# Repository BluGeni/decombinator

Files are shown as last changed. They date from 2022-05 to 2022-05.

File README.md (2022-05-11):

# Lock Decombinator

From [NerdLab Projects](https://nerdlabprojects.com/projects/8)

May 9, 2022

Step screenshot

> *Updated at: May 10, 2022*

A fun exercise to brute for a master lock combination if you forgot it.

This has been an idea of mine that I have wanted to build ever since forgetting a combo for one of my locks. Yes I know there are ways to limit the amount of combinations down to a manageable amount, but what fun is that?

### Tools Used:

 * 3D printer - I have an old modified Maker select
 * [Cheap Hobby File Set](https://amzn.to/3KXW656)
 * [Hatchbox PLA filament](https://amzn.to/3Pak0h6) (my preferred filament)
 * [Soldering Iron](https://amzn.to/3w6ndXP) - I really like the cordless version from Hakko
 * Allen wrench - 2.5mm (optional)

### Materials Used:

 * Masterlock combination lock ([If you don't have one and want to buy a cheap $3 one](https://amzn.to/38brHDk))
 * [Jumper wires](https://amzn.to/3w86KAQ)
 * [OLED I2C Display Module](https://amzn.to/3FsKS7H)
 * [ELEGOO UNO R3 Board ATmega328P](https://amzn.to/3KXThBf)
 * [MG996R 55g Metal Gear Torque Digital Servo Motor](https://amzn.to/3snNUEW)
 * 3 buttons/switches (If you dont have these on hand, [here](https://amzn.to/3kTEJrH) is an assortment package.)
 * 2x 10k resistors (More resistors than you will ever need [here](https://amzn.to/39BDNWr).)
 * [Perf Board](https://amzn.to/3L1ywo6) or any [bread board](https://amzn.to/3LXjiSo)
 * [Cheap stepper motor with driver](https://amzn.to/3kVdkWo)
 * 2x m3 hex bolt and nut - [Great variety pack](https://amzn.to/3vXJ6Ze)

### Files:

 * [Decombinator v44.f3z](./physical/Decombinator%20v44.f3z)
 * [Decombinator v44.step](./physical/Decombinator%20v44.step)
 * [Base.stl](./physical/Base.stl)
 * [servo mount.stl](./physical/servo%20mount.stl)
 * [Stepper Mount.stl](./physical/Stepper%20Mount.stl)
 * [Plunger.stl](./physical/Plunger.stl)

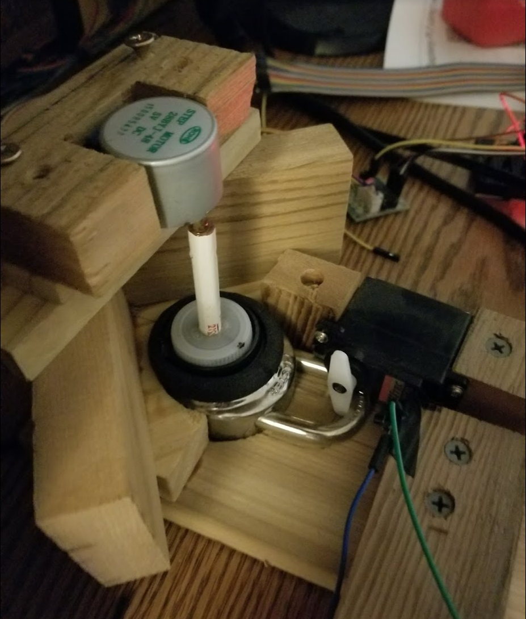
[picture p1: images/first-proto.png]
First prototype


Very first prototype from years ago that was more or less a fail do to lack of programming/design/building skills

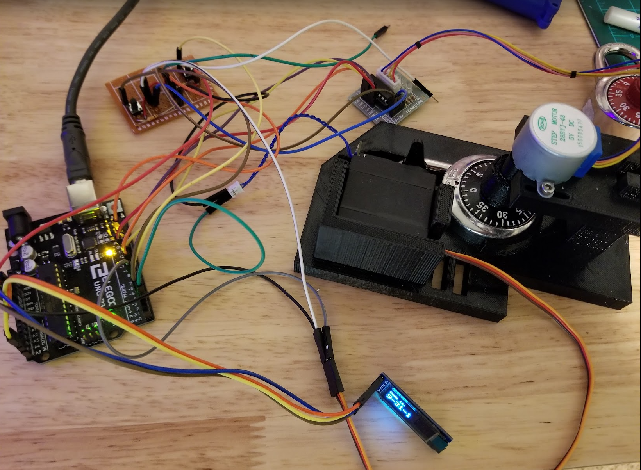
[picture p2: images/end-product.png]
Current iteration


New successful end product 

### Opening a lock

https://www.youtube.com/watch?v=IJM78OVHWlk

### Perfboard

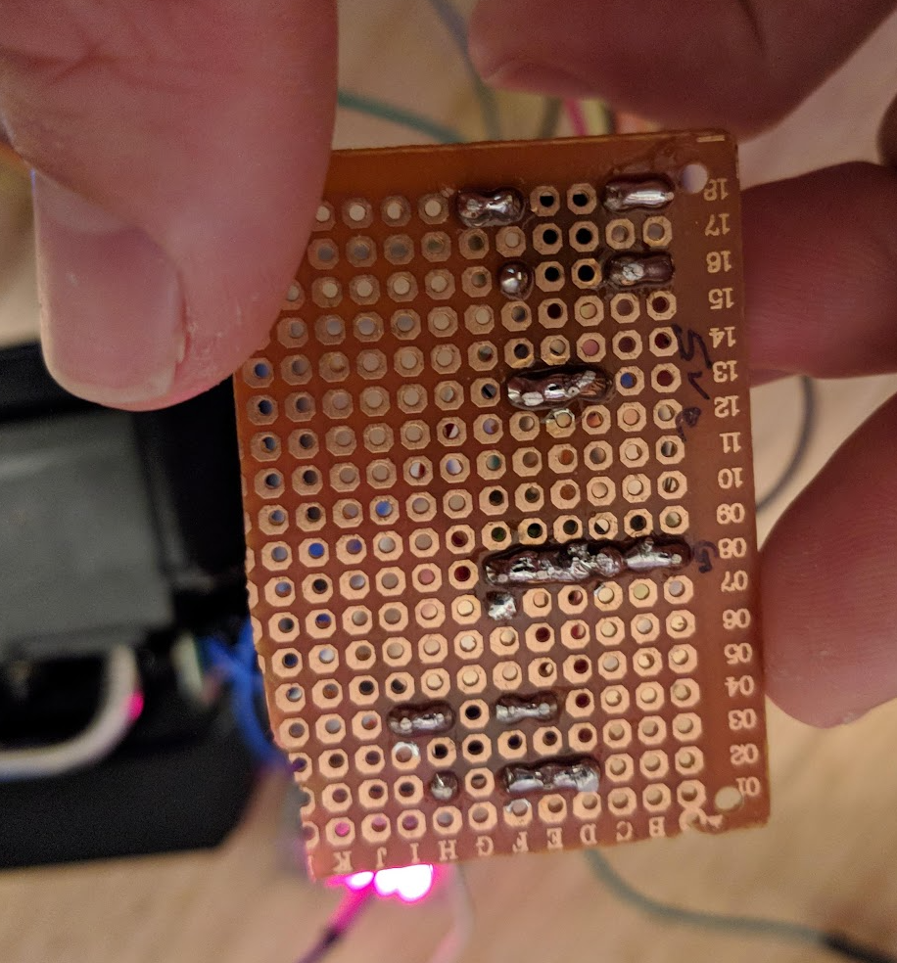
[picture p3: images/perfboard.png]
Perfboard


### How to use

After wiring it all up and starting the Arduino, use the right button switch to move the combo until it is on 0. Once there, you will click the other switch to start the decombination. The LCD screen should show which combo it is trying and display the last combo tried if it opens the lock.

### Circuit

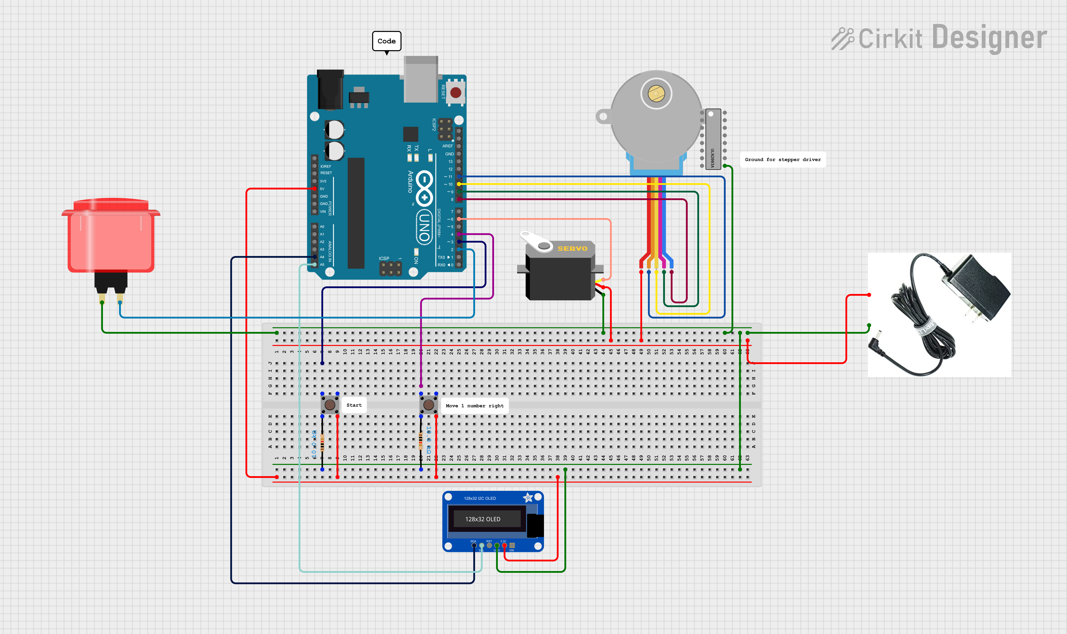
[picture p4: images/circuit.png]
Circuit


### Building

Browse to your Arduino sketch directory, and clone this repo into a subdirectory called `decombo`, e.g.,

```bash
cd ~/Arduino
git clone https://github.com/BluGeni/decombinator.git decombo
```

Then, launch Arduino, load up the `decombo` sketch from your sketchbook, and click "Verify".

> Note: [VSCode can be configured to have way more passive dev-friendly features for Arduino](./VSCode.md).

### Things learned/Struggles:

 * Pins 2 and 3 are the only pins you can use for interrupts.
 * There are 2038 steps per rev in the stepper motor I used - not 2048 like some tutorials said.
 * If your stepper motor is not super strong, attempting to open the lock will sometimes move the number a half number.
 * Ran into a lot of memory issues with all the combinations as a String array.  [Fordi](https://github.com/Fordi) helped me solve that.

References:

* https://jonwestfall.com/wp-content/uploads/2007/08/mlock1.pdf
* https://epow0.org/~amki/car_kit/Datasheet/ELEGOO%20UNO%20R3%20Board.pdf
* https://www.youtube.com/watch?v=l9Kbr8cPqOE - soldering perfboard

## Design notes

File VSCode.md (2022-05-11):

# How to use VSCode with Arduino

1. Have Arduino installed.  This is straightforward on Windows and OS-X.  On Linux, download the tarball and extract it to `/opt`, e.g.,
    ```bash
    sudo tar -C /opt -xJvf arduino-1.8.19-linux64.tar.xz
    ```

2. In VS Code, hit `<Ctrl+Shift+X>`, search for, and install:
    * `vscode-arduino`

3. *Linux*: Hit `<Ctrl+,>` to load up settings, click the "Open Settings (JSON)" button at the top-right, and add the following (version number may be different for you):
    ```json
    "arduino.path": "/opt/arduino-1.8.19",
    "arduino.commandPath": "arduino"
    ```

4. Close VS Code
5. Open this sketch's directory in VS Code, then open `decombo.ino`
6. On the bottom bar, you'll see `<Select Board>`, click it and pick your board (or any board, really).
7. Verify / compile the `ino` file by pressing `<Ctrl+Alt+R>`.

At this point, VSCode should be set up to work on Arduino code.  You'll get redlines, be able to `<F2>` rename identifiers, `<F12>` lookup definitions, `<Shift+F12>` find references, auto-manage git stuff, etc.

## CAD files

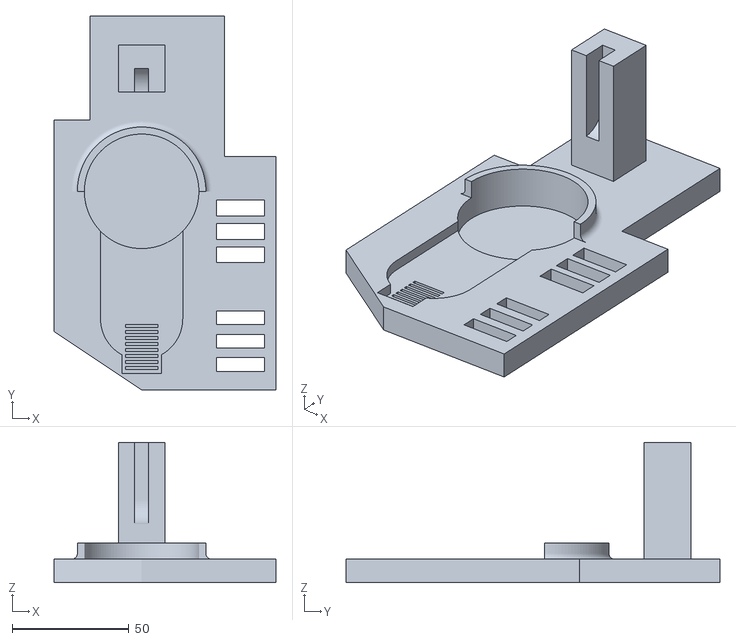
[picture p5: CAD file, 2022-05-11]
physical/Base.stl
95.0 x 160.0 x 60.0

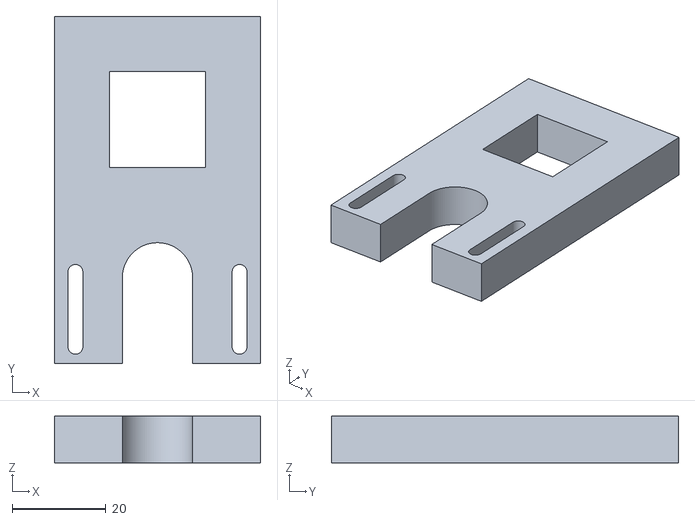
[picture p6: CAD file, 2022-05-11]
physical/Stepper Mount.stl
44.0 x 74.0 x 10.0

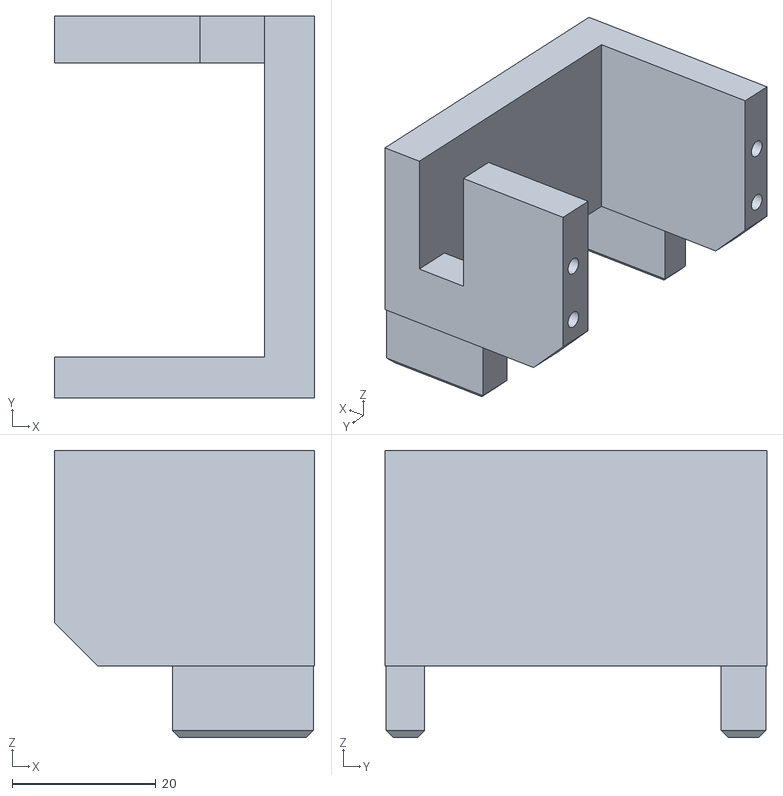
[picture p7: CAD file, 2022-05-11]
physical/servo mount.stl
36.3 x 53.2 x 40.0

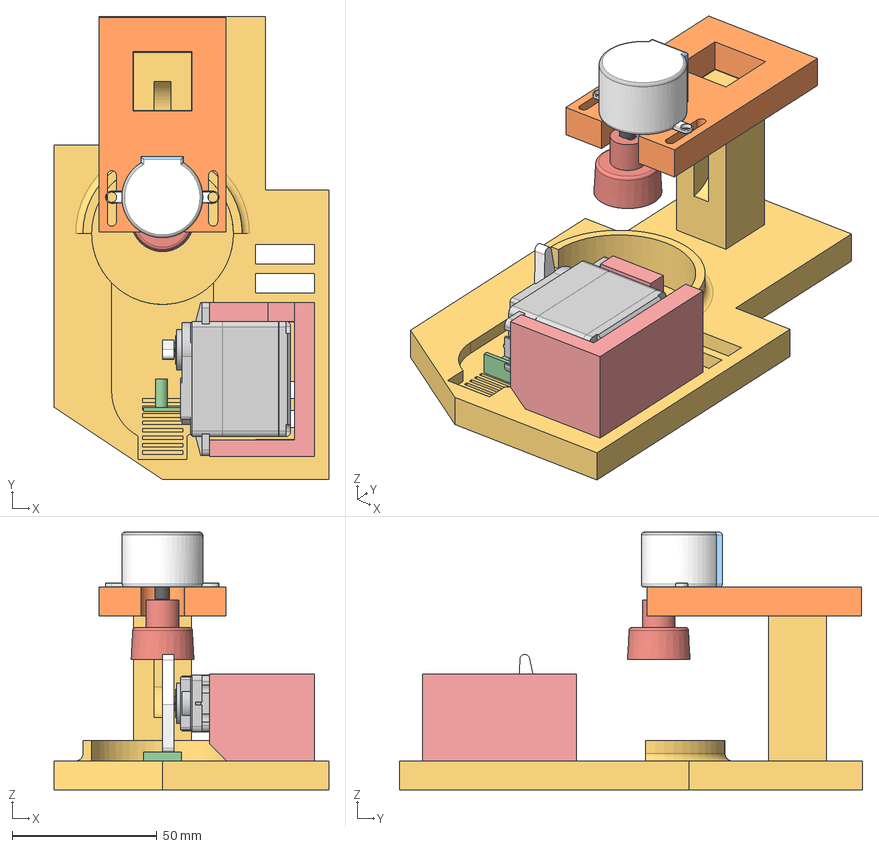
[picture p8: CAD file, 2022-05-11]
physical/Decombinator v44.step
95.0 x 160.0 x 89.0 mm
servo mount
Stepper Mount
Plunger
Slide button
Servo attachment
Base

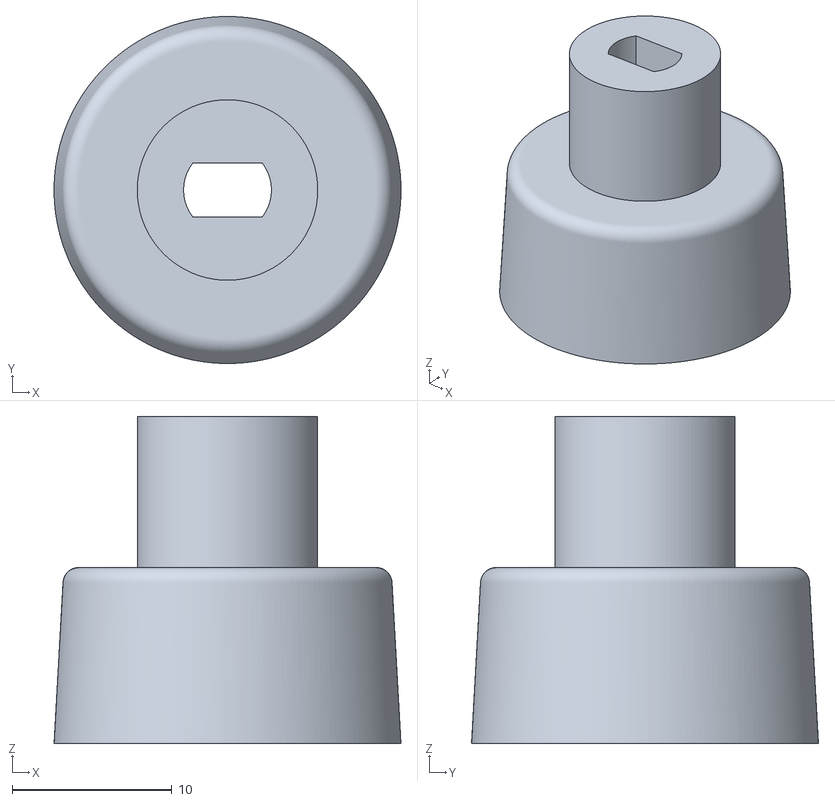
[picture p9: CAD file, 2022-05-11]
physical/Plunger.stl
21.7 x 21.7 x 20.5

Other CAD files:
physical/Decombinator v44.f3z

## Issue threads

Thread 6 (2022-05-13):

Program will not run/button doesn't respond

byrnes-patrick, 2022-05-13:
I seem to be experiencing some issues with the code. Using the code from your [site](https://nerdlabprojects.com/projects/8) seems to work (i.e. the oled shows the current number being tested and all buttons respond as they should). I didn't see any pin changes between the two versions.

Issues I am experiencing with the code on github:

1. When I am done uploading the code, the serial monitor is continuously showing "Decombinator" and doesn't stop.
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

2. There is no response from the start button at all (the other buttons, (move and combo found) seems to respond)
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

Here is the serial output from the other version:
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

BlakesMakes, 2024-12-03:
Did you ever get it to work?

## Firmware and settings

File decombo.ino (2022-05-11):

#include "config.h"
#include "src/display.h"
#include "src/dial.h"
#include "src/clasp.h"
#include "src/buttons.h"
#include "src/decombo.h"
#include "src/debug.h"

void setup() {
  initButtons();  
  initClasp();
  initDisplay();
  initDial();
  DEBUG_INIT;
}

void loop() {
  displayMessage("Decombinator");

  if (startPressed()) {
    DEBUG("Start Pressed");
    bruteForce();
  }

  if (rightPressed()) {
    DEBUG("move 1 number right");
    moveDialBy(-1);
    // Make the new position "zero"
    setDialZero();
    // Give the user time to let go of the button
    delay(100);
  }
}

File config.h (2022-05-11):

#ifndef CONFIG_H
#define CONFIG_H

// To enable SSD1306
// If you just want a lock brute and don't care about displaying the code,
// or you plan on using serial as your feedback, you can disable this.
#define DISPLAY_SSD1306

// To enable interface output to serial, uncomment
#define DISPLAY_SERIAL

// Vars needed for an SSD1306 display
#ifdef DISPLAY_SSD1306
  // Edit the following file to configure an SSD1306 display
  #include "config_ssd1306.h"
#endif

// TODO: other displays and their concerns

// Stepper motor config

// Pins
#define STEPPER_PIN1 8
#define STEPPER_PIN2 10
#define STEPPER_PIN3 9
#define STEPPER_PIN4 11

// Varies per stepper, and is often not what's on the datasheet.
#define STEPS_PER_REVOLUTION 2038

// Stepper speed
#define STEPPER_RPM 12

// Pin number for the servo
#define SERVO_PIN 6

// Servo value for "try to open the lock"
#define SERVO_OPEN 100

// Servo value for "stop trying"
#define SERVO_IDLE 10

// Pin number for the "move right" button
#define RIGHT_BUTTON_PIN 4

// Pin number for the "start" button
#define START_BUTTON_PIN 3

// Pin number for the "unlock" button / sensor
#define UNLOCK_BUTTON_PIN 2

// Comment out to disable the serial debug output
#define DEBUGGING

#endif
